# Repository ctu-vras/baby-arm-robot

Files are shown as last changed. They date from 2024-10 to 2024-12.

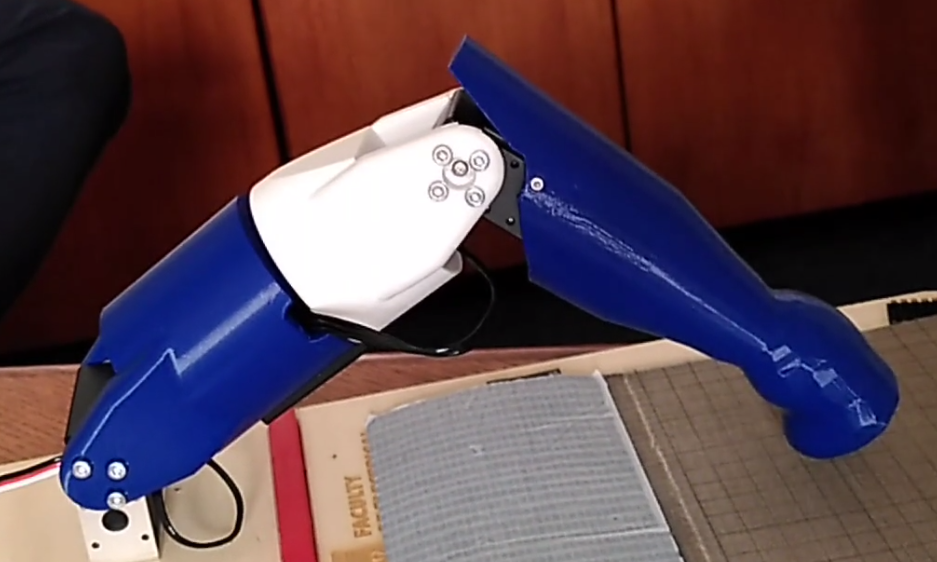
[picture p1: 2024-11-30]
JehanneArm_Thumbnail.png

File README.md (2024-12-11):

# Baby Arm Robot

IMAGE ALT TEXT (https://www.youtube.com/watch?v=AjOH3sJS-HM "A 3D printed Baby Arm")

## 1. The Essential 
Run the demonstration program   

 Prerequisites:   
- Arduino IDE  
- Python  
- Nothing should be connected (make sure to disconnect the robot's power)  

### Step 1:   
* In Arduino, install the board manager “esp32” by Espressif Systems, version 3.0.5.  
* To upload the program, select the board “ESP32 Wrover Kit (all versions).”  

### Step 2:   
* Install the **modified “SCServo” library** on your computer (For installation via the Arduino IDE, see [docs.arduino.cc](https://docs.arduino.cc/software/ide-v2/tutorials/ide-v2-installing-a-library/)).  
* Install the programs *“Random_movement.ino”*, *“Read_Data_Random_Movement.py”* and *“simple_read.py”*  
**Notes 1 :** The examples can help you understand how to use the library functions.  
  - ID = 254 selects all motors.  
  - The added function is  "servoReset(ID); ".  
**Notes 2 :** There is more information about the modified library below.

### Step 3:   
* On Linux, open the terminal and run the command  __ls /dev/tty*__. Then connect the robot and run the command  "ls /dev/tty* " again. Note the new serial port that appears. This is the serial port associated with the robot, which should be used in Arduino. Generally, it will be something like  *"port_robot = "/dev/ttyUSB0"*.  
* Without disconnecting the robot, now connect the false skin, then run the command  __ls /dev/tty*__ again. Note the new serial port that appears. This is the serial port associated with the false skin. Generally, it will be something like  *"port_skin= "/dev/ttyUSB1"*.  
* In the Python program *“simple_read.py”*, on line 11, set:  
 __python arduino = serial.Serial(port="port_robot", baudrate=115200, timeout=0.1)__  
* In *“simple_read.py”* on lines 20/21, set:  __
python port2=port_skin__  (or port1 = port_skin) 
* In the Python program *“Read_Data_Random_Movement.py”* on line 7, set:  
__python ser = serial.Serial(port="port_robot", baudrate=115200, timeout=0.1)__

### Step 4:   
* Upload the program to the board and close the Arduino terminal if it is open.  
* In two separate terminals, run the programs  *"simple_read.py"* and  *"Position_Motor_Forward.py"*.  
Connect the robot board to the power generator.  

**And that's it—the robot is working.**  

**Notes:** 
* Having the serial monitor open in Arduino can cause communication issues with the serial ports.  
* Motor link (ST3025): [https://www.waveshare.com/wiki/ST3025_Servo](https://www.waveshare.com/wiki/ST3025_Servo)

## 2. If you want to know more about how the robot was construct. 

### 2.1. Joints Vocabulary

In this part, we will see which joints and which amplitudes were chosen for the robot arm. To do this, it is important to understand how the human body is described in space. Also, it is necessary to start by describing the anatomical reference position of the human body.

<p align="center">
  
  <br> Figure : Anatomical Position Reference
</p>

 Here, it is the position of the arm that interests us. Also the arm in anatomical reference position, corresponding to 0° amplitude, is considered as the point of origin of shoulder movements. From this neutral position, the range of movement of the shoulder is measured in the different directions, which makes it possible to quantify the angular displacements for each movement (flexion, extension, abduction, etc.).

Now that we have the anatomical reference position, we can define the axes and planes of movement using the document below :

<p align="center">
  
  <br> Figure : Axes and planes of movement
</p>

This allows the movements to be defined as follows :

<p align="center">
  
  <br> Figure : Definition of differents types of movements
</p>

The arms have many joints, however we will focus only on those that interest us: the elbow and the shoulder. The question of having connections at the wrist was raised but quickly dismissed because the baby often keeps his fists closed and uses his wrists little and only with small ranges of movement. This connection has little impact on the general movement of the infant's arm.

### 2.2. Elbow Joints

The elbow allows two main types of movements, each with specific amplitudes

***1. Flexion and Extension :*** The elbow flexion occurs when the forearm approaches the arm and has a maximum amplitude of 160°. During the extension, on the contrary, the forearm moves away from the arm, extending the arm in a straight line, the amplitude of the extension is approximately 4° in an infant.
**2. Internal rotation and external rotation :** Internal rotation commonly called pronation for the hands allows the palm of the hand to be turned downward by approximately 180°, while external rotation called supination for the hands turns the palm upward by a maximum of 45°.

### 2.3. Shoulder Joints

The shoulder is a complex joint that allows us to perform many movements with a large amplitude. Here is an overview of the main movements of the shoulder and their amplitudes [1] and [2].

***1. Flexion and extension :*** Flexion of the shoulder corresponds to raising the arm forward, while extension brings the arm back. These movements occur in the sagittal plane, with flexion up to 180° and extension up to about -90° for an infant under two years old.

**2. Abduction and adduction :** Abduction corresponds to the movement of the arm away from the body to the side, while adduction brings the arm back towards the trunk. Abduction allows the arm to be raised up to approximately 180° in the frontal plane.

***3. Internal rotation and external rotation :*** Internal (or medial) rotation allows the arm to be turned inward approximately 180° toward the torso, while external (or lateral) rotation allows the arm to be turned outward approximately 45°. This movement occurs at the humerus and allows the hand and forearm to be oriented in different directions.

**4. Circumduction :** This movement is a combination of flexion, extension, abduction, and adduction, allowing the shoulder to trace a complete circle. Circumduction allows the shoulder to be mobilized in almost any direction and provides the freedom of movement necessary for gestures such as throwing or catching.

### 2.4. Choice of joints

According to the specifications, the robot must have 2 to 3 degrees of freedom to reproduce basic shoulder and elbow movements, inspired by the natural movements of infants. Also for the rest of the project, we strategically chose the **elbow flexion**, **shoulder flexion** and **shoulder rotation** movements, in particular because these are the main movements made by babies in self-touching gestures and exploration of their body. In addition, by allowing the robot to bend and extend its arm at the elbow, its ability to reach objects at different distances without moving the entire arm is improved, which is important because the 2D touch surface can be fragile, so controlling the force applied to it is essential. Shoulder flexion allows the entire arm to be raised or lowered. This movement is important for directing the arm up or down, thus increasing the robot's vertical range of action. Finally, flexion uses simple, robust and easy-to-maintain linear or rotary mechanisms, which increases its reliability for repetitive tasks and can reduce maintenance costs if necessary. However, even if flexion is advantageous, it is essential for us to rotate the robot arm, in order to be able to reach lateral positions and adjust the orientation of the hand and forearm. Thanks to rotation, the robot can interact with the skin at different angles, which is essential for the complex movements that we are trying to reproduce and which require three-dimensional adaptation.

Here are the movements that we have chosen to keep for the robot and the angular range that corresponds to them and that was tested on the robot:
- Generation of a random position for **motor 1** in the interval **[650, 1561]** or **80°** of freedom - **Elbow flexion**.
- Generation of a random position for **motor 2** in the interval **[3000, 3776]** or **68.2°** of freedom - **Shoulder rotation**.
- Generation of a random position for **motor 3** in the interval **[1000, 2000]** or **87.9°** of freedom - **Shoulder flexion**.

**Bibliography :** 
- [1]  PHYSICAL MEDICINE & REHABILITATION PEDIATRIC RANGE of MOTION Chapter 16 published on Aug 10, 2016
- [2] Range of motion measurements: reference values and a database for comparison studies J. M. SOUCIE, C. WANG, A. FORSYTH, S. FUNK, M. DENNY, K. E. ROACH, D. BOONE, THE HEMOPHILIA TREATMENT CENTER NETWORK published the 11th November of 2010

## 3. ST3025 - Motors

Library Présentation : SCSServo
SCSServo, available on waveshare wiki, is the library associated with ST3025 motors usable on Arduino. This library uses an asynchronous serial communication protocol. Only the sms_sts mode of the library is used, there is a list of the main functions present :

### 3.1. Functions for basic configuration and control :
- CalibrationOfs(int ID): Calibrates the current motor position as its neutral position (new offset).
- Ping(int ID): Checks the connection with the motor by returning its ID if it is accessible.
- unLockEprom(ID): Unlocks access to the protected parameters (EEPROM) of the motor with the specified ID, allowing their modification.
- LockEprom(ID): Locks the EEPROM again after modifications to protect the parameters from accidental changes.
- writeByte(ID, PARAM, VALUE): Modifies a parameter of the motor. It changes the PARAM parameter of the target motor ID to a new value VALUE.

### 3.2. Commands to write positions:
- WritePosEx(int ID, int Position, int Speed, int ACC): Moves motor ID to a given position with a defined speed and acceleration.
- RegWritePosEx(int ID, int Position, int Speed, int ACC): Prepares a position command for a given motor, but waits for a group instruction (RegWriteAction) to execute. This allows the movements of multiple motors to be synchronized.
- RegWriteAction(): Simultaneously executes all commands prepared by RegWritePosEx.
- SyncWritePosEx(byte ID[], int Num, s16 Position[], u16 Speed[], byte ACC[]): Commands multiple motors to move simultaneously to respective positions with specified speeds and accelerations.

### 3.3. Functions to read motor states
- FeedBack(int ID): Retrieves the current parameters of a given motor (position, speed, load, voltage, temperature, motion status, and current).
- ReadPos(int ID): Reads the current position of the motor.
- ReadVoltage(int ID): Reads the current supply voltage of the motor.
- ReadTemper(int ID): Reads the internal temperature of the motor.
- ReadSpeed(int ID): Reads the current speed of the motor.
- ReadLoad(int ID): Reads the load applied to the motor.
- ReadCurrent(int ID): Reads the current consumed by the motor.
- ReadMove(int ID): Checks if the motor is moving.

Additionally, the recommended communication speed with the servo driver is 115200 bits per second on the serial line. This speed, called baudrate, is configured at the beginning of each arduino code.

### Library Modification 

The functions described in the previous part take over the available instructions of the serial protocol except the RESET instruction. 

<p align="center">
  
  <br>Figure : Description of the instruction RESET in the file Communication Protocol User Manual
</p>

For the use of the robot it is important to add the **RESET** instruction that allows to deactivate the motor torque by removing the power supply to the motor without disconnecting the entire board. Thus, the motor no longer opposes active resistance, leaving only the natural mechanical resistance. The objective is to reduce the risk of damaging the components of the robotic arm and the tactile skin that could be damaged by excessive force from the motors.

Thus, the functions needed to use the **RESET** instruction (0x06) in the standard and serial mode of the servomotors have been added in the corresponding source files :

	INST.h : 	#define INST_RESET 0x06 ;
In this file we define a constant that associates the **INST_RESET** command with the hexadecimal value 0x06. 0x06 being the identifier of the reset instruction in the serial communication protocol, it is this value that will be transmitted to the servo driver to indicate that the operation to be performed is a reset.

	SCS.h :		int resetServo (u8 ID);
The previous line is the prototyping of the **resetServo()** method. The **resetServo()** method is accessible to all other parts of the library source code because they all include the SCS.h header file.

	SCS.cpp :
	int SCS :: resetServo(u8 ID)
	{
		rFlushSCS();
		writeBuf(ID, 0, NULL, 0, INST_RESET);
		wFlushSCS();
		return Ack(ID);
	}

Here, the **resetServo()** function is the actual implementation of the function declared in SCS.h. The **rFlushSCS()** functions are used to read and flush the read buffer. The goal is to prepare the system to receive or write new data without interfering with previous data. The **writeBuf()** function sends the **INST_RESET** constant (defined in the inst.h file) specifying the ID of the servomotor that must be reset. The parameters ‘0’, NULL and ‘0’ indicate that there is no data to memorize. The **wFlushSCS()** function is used to flush and send the write buffer to the servomotor, which ensures that the command is transmitted. Finally, the resetServo() function returns the **Ack()** function which ensures that the servomotor has received the command and responded correctly. The **Ack()** function thus returns a success code ‘0’ if the reset was performed correctly and an error code if something failed.

	SMS_STS.h : 	
	class SMS_STS : public SCSerial {
	public:
	...
	virtual int resetServo(u8 ID);
	private: 
	... };

Here, we declare a virtual method in the **SMS_STS class** which is a derived class of SCSerial. The **SMS_STS** class is specialized in controlling and managing servo motors and uses the basic serial communication provided by the SCSerial class. The SCSerial class itself is derived from the SCS class and acts as an interface for managing servo motors. The **resetServo()** method takes as a parameter the identifier of the motor to be reset and returns an integer to indicate an error ‘1’ or the success ‘0’ of the reset. This method is an interface to reset a servo motor with a given ID and is defined in the file “SMS_STS.cpp”.

	SMS_STS.cpp : 	
	int SMS_STS::resetServo(u8 ID)
	{
		return SCSerial::resetServo(ID);	
	}

The **SMS_STS::resetServo(u8 ID)** method calls a similar **resetServo()** method belonging to the SCSerial class, which is the parent class responsible for serial communication with servo motors. However, the SCSerial class is itself derived from the SCS class. It is therefore in the SCS.h and SCS.cpp files that the **resetServo()** function was prototyped and defined.

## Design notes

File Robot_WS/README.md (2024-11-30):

# Video demonstration

Check the Baby arm video (https://youtu.be/AjOH3sJS-HM?si=Y8BSaiP-1UWCQKFR)

# How to run

Run the demonstration program

Prerequisites:

\- Arduino IDE

\- Python

\- Nothing should be connected (make sure to disconnect the robot\'s
power)

Step 1:

- In Arduino, install the board manager ["]{dir="rtl"}esp32" by
  Espressif Systems, version 3.0.5.

- To upload the program, select the board ["]{dir="rtl"}ESP32 Wrover Kit
  (all versions)."

Step 2:

- Install the modified ["]{dir="rtl"}SCServo" library on your computer
  (For installation via the Arduino IDE, see
  \[docs.arduino.cc\](https://docs.arduino.cc/software/ide-v2/tutorials/ide-v2-installing-a-library/)).

- Install the programs ["]{dir="rtl"}Random_movement.ino,"
  "Read_Data_Random_Movement.py," and ["]{dir="rtl"}simple_read.py."

- Note: The examples can help you understand how to use the library
  functions.  
  - ID = 254 selects all motors.  
  - The added function is \"servoReset(ID); \".

Step 3:

- On Linux, open the terminal and run the command \"*ls /dev/tty\** \".
  Then connect the robot and run the command \"*ls /dev/tty\** \" again.
  Note the new serial port that appears. This is the serial port
  associated with the robot, which should be used in Arduino. Generally,
  it will be something like \"port_robot = \"/dev/ttyUSB0\".

- Without disconnecting the robot, now connect the false skin, then run
  the command \"*ls /dev/tty\** \" again. Note the new serial port that
  appears. This is the serial port associated with the false skin.
  Generally, it will be something like \"port_skin= \"/dev/ttyUSB1\".

- In the Python program ["]{dir="rtl"}simple_read.py," on line 11,
  set:  
  python arduino = serial.Serial(port=\"port_robot\", baudrate=115200,
  timeout=0.1)

- In ["]{dir="rtl"}simple_read.py," on lines 20/21, set:  
  python port2 = port_skin (or port1 = port_skin)

- In the Python program ["]{dir="rtl"}Read_Data_Random_Movement.py," on
  line 7, set:  
  python ser = serial.Serial(port=\"port_robot\", baudrate=115200,
  timeout=0.1)

Step 4:

- Upload the program to the board and close the Arduino terminal if it
  is open.

- In two separate terminals, run the programs \"simple_read.py \" and
  \"Position_Motor_Forward.py \".

- Connect the robot board to the power generator.

And that\'s it---the robot is working.

Notes:

- Having the serial monitor open in Arduino can cause communication
  issues with the serial ports.

- Motor link (ST3025):
  \[https://www.waveshare.com/wiki/ST3025_Servo\](https://www.waveshare.com/wiki/ST3025_Servo)

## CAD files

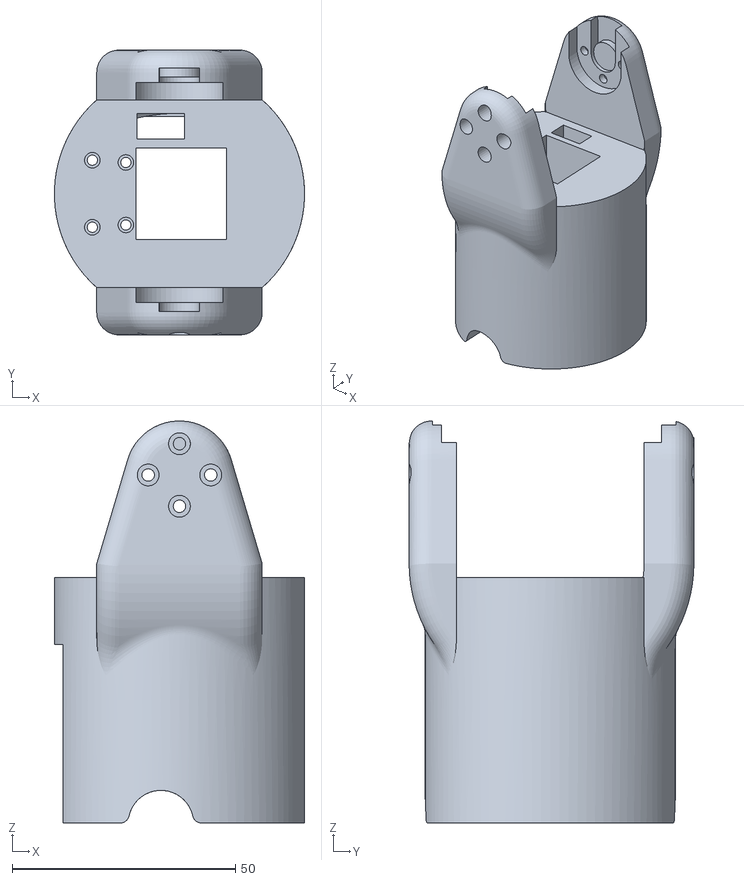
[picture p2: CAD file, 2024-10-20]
Robot_WS/Robotic_Arm_CAD/STL/LOWER_ARM_SHOULDER.stl
56.0 x 63.8 x 90.0

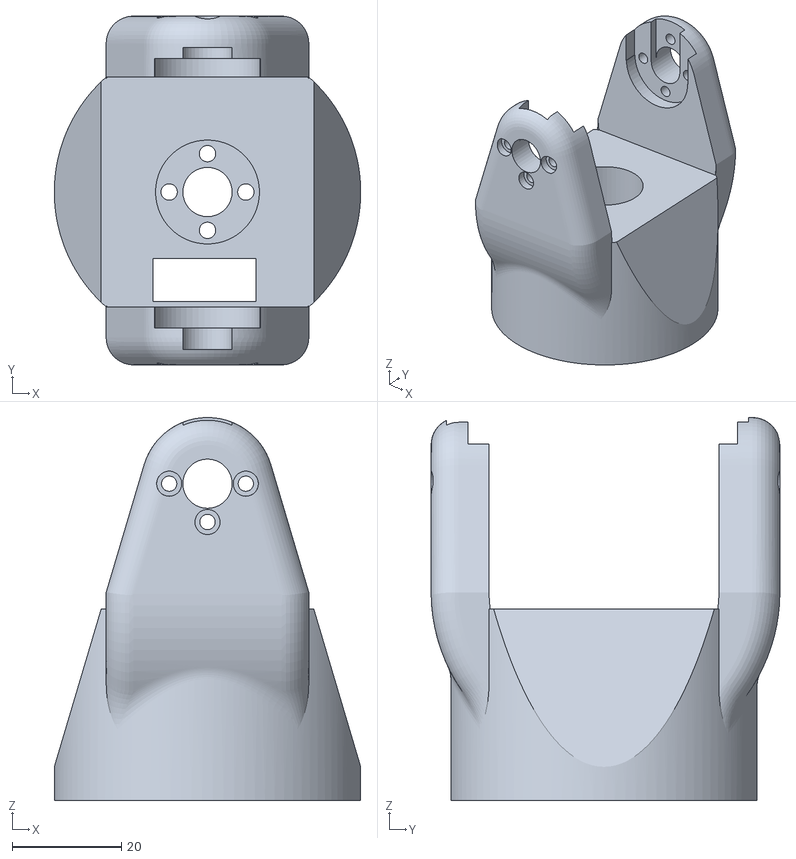
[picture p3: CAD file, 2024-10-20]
Robot_WS/Robotic_Arm_CAD/STL/LOWER_ARM_ELBOW_TEST.stl
56.0 x 63.8 x 70.0

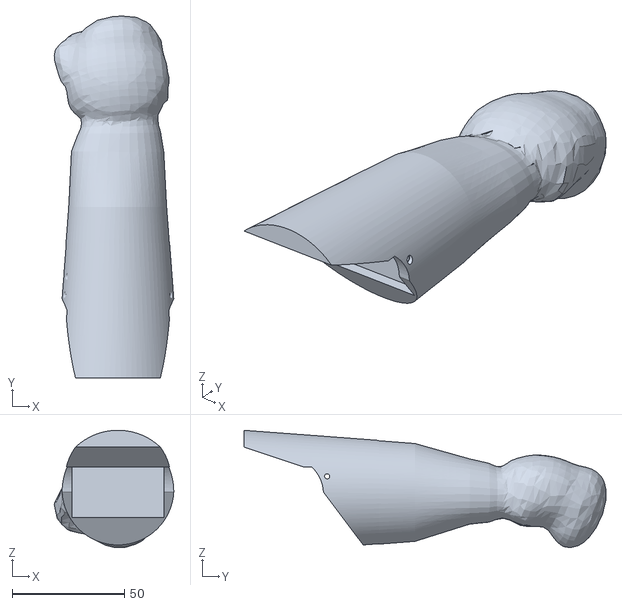
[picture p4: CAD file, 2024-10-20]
Robot_WS/Robotic_Arm_CAD/STL/Upper_arm_v2.stl
53.2 x 161.0 x 52.2

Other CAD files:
Robot_WS/Robotic_Arm_CAD/Fusion/LOWER_ARM_ELBOW_TEST.f3d
Robot_WS/Robotic_Arm_CAD/Fusion/LOWER_ARM_SHOULDER.f3d
Robot_WS/Robotic_Arm_CAD/Fusion/Upper_arm_v2.f3d

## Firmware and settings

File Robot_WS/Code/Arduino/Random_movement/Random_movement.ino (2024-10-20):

#include <SCServo.h>


SMS_STS sms_sts;


// the uart used to control servos.
// GPIO 18 - S_RXD, GPIO 19 - S_TXD, as default.
#define S_RXD 18
#define S_TXD 19


unsigned long previousMillis = 0;  // Variable to store last time position was read
const long interval = 1000;         // Interval at which to read position (in ms)


void setup() {
  Serial.begin(115200);
  Serial1.begin(1000000, SERIAL_8N1, S_RXD, S_TXD);
  sms_sts.pSerial = &Serial1;
  delay(1000);
}


void loop() {
  unsigned long currentMillis = millis();


  // Read the servo position every 'interval' milliseconds
  if (currentMillis - previousMillis >= interval) {
    previousMillis = currentMillis;

    int Pos1;
    int Pos2;
    int Pos3;
    int Load1;
    int Load2;
    int Load3 ;

    Pos1 = sms_sts.ReadPos(1);  // Get the position of the servo with ID 1
    Pos2 = sms_sts.ReadPos(2);  // Get the position of the servo with ID 2
    Pos3 = sms_sts.ReadPos(3);  // Get the position of the servo with ID 3

    Load1 = sms_sts.ReadLoad(1);  // Get the position of the servo with ID 
    Load2 = sms_sts.ReadLoad(2);  // Get the position of the servo with ID 3
    Load3 = sms_sts.ReadLoad(3);  // Get the position of the servo with ID 3

    //Pos1 = sms_sts.ReadMode(2);
    //Pos3 = sms_sts.EnableTorque(2,0);

    // Serial.print("Position  : ");
    // Serial.print(Pos1);
    // Serial.print(", Position 2 : ");
    // Serial.print(Pos2);
    // Serial.print(", Position 3 : ");
    // Serial.println(Pos3);

    // Serial.print("Load 1 : ");
    // Serial.print(Load1);
    // Serial.print(", Load 2 : ");
    // Serial.print(Load2);
    // Serial.print(", Load 3 : ");
    // Serial.println(Load3);



    if (abs(Load1)>24 || abs(Load2)>250 || abs(Load3)>250){
      sms_sts.resetServo(254);

      // Serial.println();
      // Serial.println("Load to high !!");
      char data = Serial.read();

      if (data=='1'){
        Serial.println("La peau a ete touchee");
        Serial.print(Pos1);
        Serial.print(",");
        Serial.print(Pos2);
        Serial.print(",");
        Serial.println(Pos3);

      }
      delay(2000);
      Position_initiale();
      sms_sts.resetServo(254);

      delay(3000);
    }

    // int Skin_touched = random(0,10);

    // if (Skin_touched>8){
    //   sms_sts.resetServo(254);
    //   delay(2000);

    //   Serial.println("La peau a ete touchee");
    //   Serial.print(Pos1);
    //   Serial.print(",");
    //   Serial.print(Pos2);
    //   Serial.print(",");
    //   Serial.println(Pos3);

    //   Position_initiale();
    // }
    if (Serial.available() > 0) {
      char data = Serial.read();
      // Serial.print("Received data: ");
      // Serial.println(data);
      
      if (data == '1') {
        sms_sts.resetServo(254);
        delay(2000);

        Serial.print(Pos1);
        Serial.print(",");
        Serial.print(Pos2);
        Serial.print(",");
        Serial.println(Pos3);

        // Serial.println(sms_sts.ReadPos(2));

        Position_initiale();

        sms_sts.resetServo(254);

        // Serial.println("La peau a ete touchee");

        // Serial.println(sms_sts.ReadPos(2));

        delay(3000);
      }

    }

  }

  //Move servo with ID 3 to two different positions without delay()
  static bool movingToPos1 = true;
  static unsigned long moveStartTime = 0;

  int Position1 = random(650, 1561);
  int Position2 = random(3000, 3776);
  int Position3 = random(1000, 2000);

  if (movingToPos1) {
    // If the servo is not yet moving to position 4095, start moving
    if (millis() - moveStartTime >= 2000) {  // Move after 2 seconds
      sms_sts.WritePosEx(1, 650, 1000, 50);  // Move to position 4095
      sms_sts.WritePosEx(2, 3776, 1000, 50);  // Move to position 4095
      sms_sts.WritePosEx(3, 2000, 1000, 50);  // Move to position 4095

      moveStartTime = millis();
      movingToPos1 = false;
    }
  } else {
    // After the move to position 4095, move back to position 2000
    if (millis() - moveStartTime >= 2000) {  // Move after 2 seconds
      sms_sts.WritePosEx(1, Position1, 1000, 50);  // Move to position 4095
      sms_sts.WritePosEx(2, Position2, 1000, 50);  // Move to position 4095
      sms_sts.WritePosEx(3, Position3, 1000, 50);  // Move to position 2000
      moveStartTime = millis();
      movingToPos1 = true;
    }
  }

  
}


void Position_initiale(){
  sms_sts.WritePosEx(1, 650, 1000, 50);  // Move to position 4095
  sms_sts.WritePosEx(2, 3776, 1000);  // Move to position 4095
  sms_sts.WritePosEx(3, 2000, 1000, 50);  // Move to position 4095

  delay(3000);

}

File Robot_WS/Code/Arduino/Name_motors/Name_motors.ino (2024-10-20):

/*
example for changing ID.
*/

#include <SCServo.h>

SMS_STS sms_sts;
// the uart used to control servos.
// GPIO 18 - S_RXD, GPIO 19 - S_TXD, as default.
#define S_RXD 18
#define S_TXD 19

int ID_ChangeFrom = 1;
int ID_Changeto   = 3;

void setup()
{
  Serial1.begin(1000000, SERIAL_8N1, S_RXD, S_TXD);
  sms_sts.pSerial = &Serial1;
  delay(1000);
  sms_sts.unLockEprom(1);//unlock EPROM-SAFE
  sms_sts.writeByte(ID_ChangeFrom, SMS_STS_ID, ID_Changeto);//ID
  sms_sts.LockEprom(ID_Changeto);//EPROM-SAFE locked
}

void loop()
{

}

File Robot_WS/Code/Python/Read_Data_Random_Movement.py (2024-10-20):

import serial
import csv
import time


# Configure the serial port
ser = serial.Serial('/dev/ttyUSB0', 115200, timeout=1)  # POZOR to choose the apropriate port cf.file config_port.py


# Open the CSV file for writing
with open('data_position.csv', 'w', newline='') as csvfile:
    csvwriter = csv.writer(csvfile)
    csvwriter.writerow(["Servo1 Position", "Servo2 Position", "Servo3 Position"]);


    try:
        while True:
            if ser.in_waiting > 0:
                # Read the serial data
                line = ser.readline().decode('utf-8').strip()
                if line:
                    print(line)  # Print the data (optional)
                    # Split the data and write to CSV
                    data = line.split(',')
                    if len(data) == 3:  # POZOR ajust the number of len(data). This condition can be remove, depending on the program you use. 
                        csvwriter.writerow(data)
    except KeyboardInterrupt:
        print("Data logging stopped.")
    finally:
        ser.close()
